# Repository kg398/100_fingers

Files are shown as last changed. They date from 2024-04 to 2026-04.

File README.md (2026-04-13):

# 100_fingers project: Parametric hand
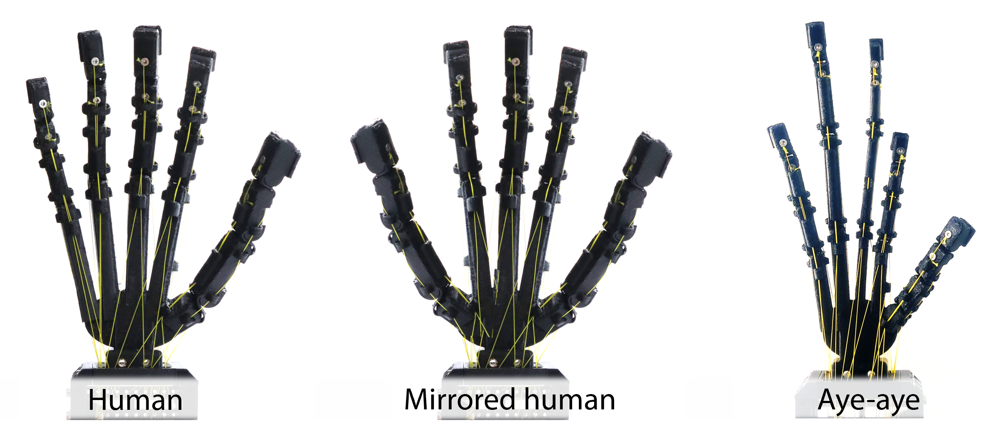
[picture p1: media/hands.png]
Human, mirrored human, and aye-aye hand designs and assemblies


Figure 1: Three example hands included in the initial release and presented in [(1)](#list-of-publications).

Generating large numbers of anatomical parameterised fingers and hands with OpenSCAD (https://openscad.org/).

## Changelog
- 10/12/2025: Overhaul of parameter definitions and modular bone generation, see section: Hand Customisation

## Intro
Code for generating the initial hand version and 3D files for reproduction and modular actuation.
The hand is designed for single-piece 3d printing with consumer-grade printers, enabling rapid customisation and large-scale real-world experimentation.
Additionally, the hand is designed to be uncomprimising with actuation. Five tendons per four degree of freedom finger allows full control. Though for simplicity, accessibility, and exploration of hand behaviours, the included actuation system examples rely heavily on underactuation by connecting the majority of tendons to passive springs.

### Summary of files
- /OpenSCAD: scripts for generating hands with OpenSCAD. parameters.scad for demo use and parameters for generating example hands
- /STLs: 3D files for 3D printable parts
  - /STLs/hands: three example hands generated from parameters.scad and example generated for visualisation (no_lig)
  - /STLs/actuation_box: 3D files for three examples of modular actuation (1 degree-of-freedom(dof)/synergy, 2 dof/synergy, 1 dof with switching modulation)
  - /STLs/manual_handles: 3D files for manual lever actuation and handles for 1 and 2 dof actuation boxes
- /build_guide: PDF, timelapse, and annotated video of build process for release v1.2
- /media: images from publication (in progress)

### Hand customisation
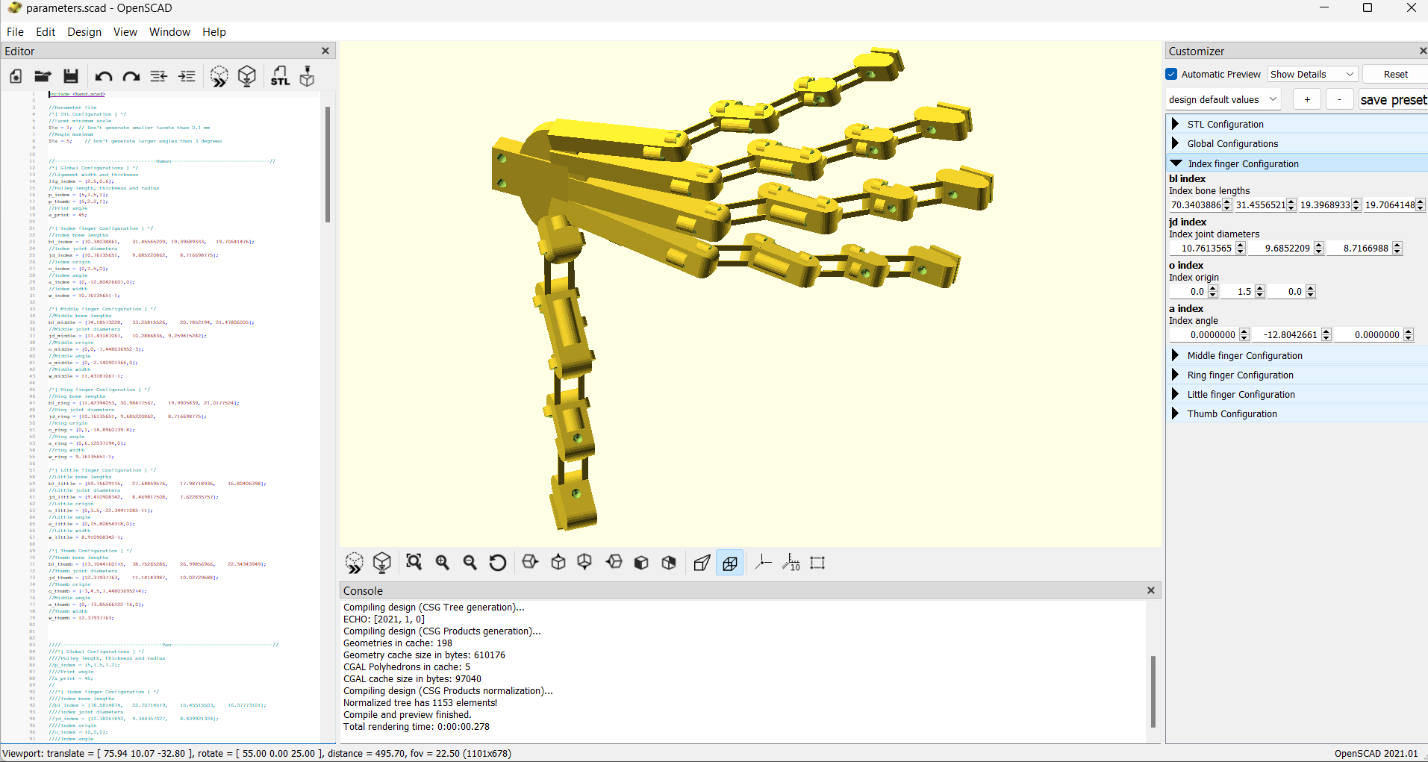
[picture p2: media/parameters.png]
Screenshot of parameters.scad in OpenSCAD


Figure 2: Hand parameters.

For basic customisation, parameters.scad can be modified to alter number of fingers/thumbs, predefined finger types (four_dof = anatomical, three_dof/two_dof = simplified examples), finger/thumb positions, orientations, curvature towards palm, all bone lengths/joint widths/diameters, pulley/ligament sizes.

For custom digits/bones built on existing primitives (e.g. for different tendon routings/degrees of freedom/no. bones), new configurations can be created (see digits.scad for configuration details). For new features, e.g. expanded types of joints/nails/etc., configurations must be extended and features manually defined in primitives.scad/modular_bone.

Parameters are separated into global and local. Three global params define number of fingers, number of thumbs and the overall hand curvature towards the palm (0 deg gives a flat hand all fingers in the same plane, 90 deg will keep fingers parallel as if wrapped around a cylinder).
Local parameters are organised into lists separated by digits (fingers vs. thumbs) and parameter types:
- finger_type: loads predefined finger configuration (four_dof = default anatomical finger). Must be at least 1 defined per n_fingers
- lig_[digit]: ligament width and thickness. If fewer pairs are defined than n_fingers, only the first pair will be used for all of that digit type
- p_[digit]: pulley length, internal radius, thickness. If fewer pairs are defined than n_fingers, only the first pair will be used for all of that digit type
- bl_[digit]: n bone lengths per digit where n is number of bones in digit type config. First element is closest to the palm 
- jd_[digit]: n+1 joint diameters per digit where n is number of bones in digit type config. First element is closest to the palm
- w_[digit]: n+1 joint widths per digit where n is number of bones in digit type config. First element is closest to the palm
- o_[digit]: 3 dof translation per digit. x = longitudinal (generally = 0), y = normal to palm, z = lateral to palm (main translation)
- a_[digit]: 3 dof rotation per digit, rx = unused, ry = digit rotation in a_print/hand curvature axis (normal to palm when a_print = 0, longitudinal axis when a_print = 90), rz = unused
  
## Fabrication instructions
### Hand assembly
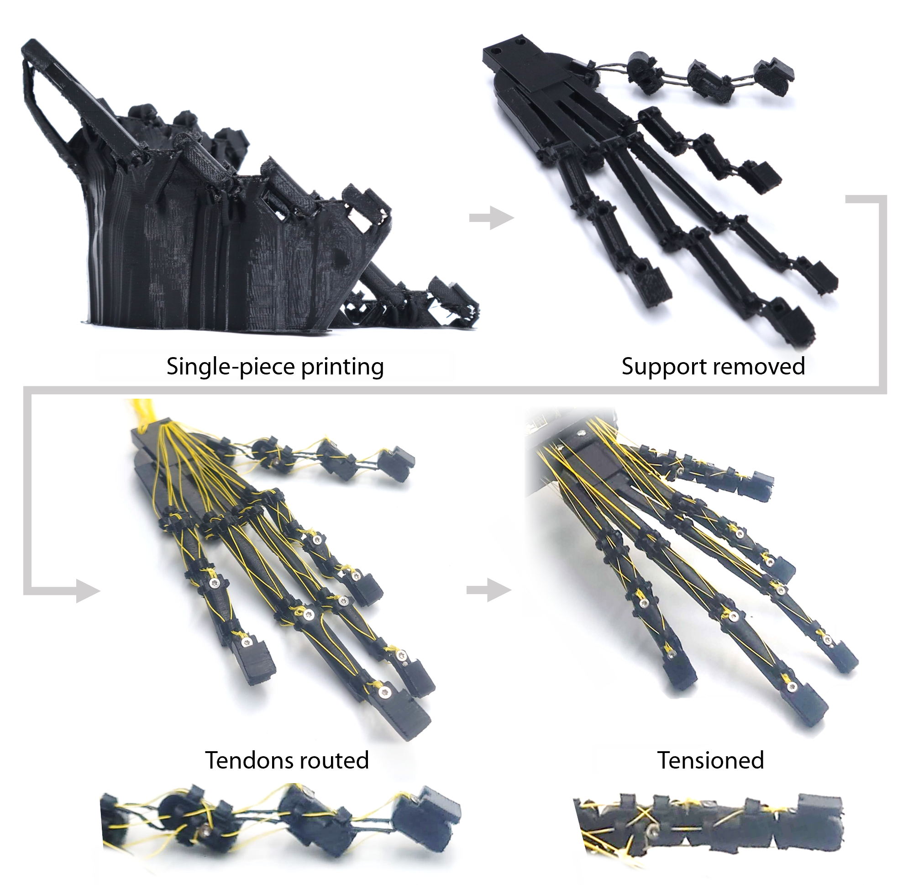
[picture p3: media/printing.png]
Steps for 3D printing and attaching tendons

Figure 3: Hand printing and assembly.

See /build_guide for more detailed fabrication tips and assembly information, and [bill of materials](#bill-of-materials) for basic acquisition requirements.

Hands can be printed via commercial FDM printers (Prusa/Creality/Craftbot/Raise3D tested). General printing requirements are: large build volume and semi-flexible materials. **Polypropylene** printing is recommended for good living hinge properties and relative ease of printing with a single extruder and standard temperatures. Print orientation is critical (palm should face down with fingertips closest to build plate and all ligament pairs flat relative to the build plate).

SLS printing is also suitable. Only polyamide (PA2200) has been tested, resulting in stiffer bones than polypropylene and a cleaner print. Orientation is less critical.

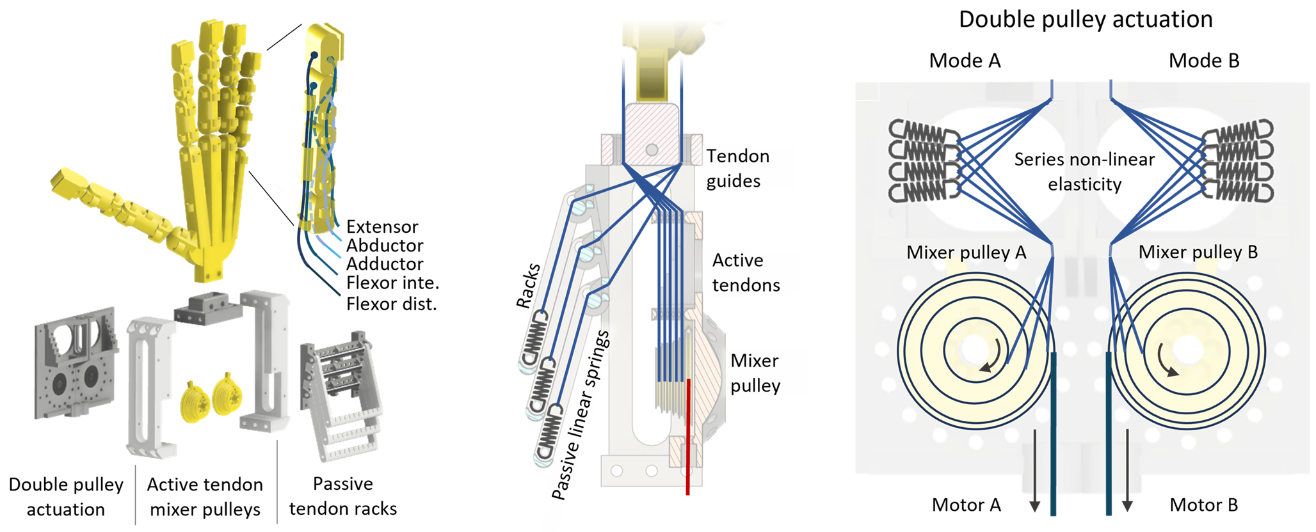
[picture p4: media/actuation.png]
Actuation box features and tendon routing paths


Figure 4: Tendon routing and actuation.

Once the hand is printed, tendons must be routed manually. Depending on application, braided nylon from 0.2--0.5mm diameter is suitable (0.2mm is easier to work with and results in less friction, though has lower load potential). Tie with self-tightening knots to countersunk M2 bolts following routing from Figure 4.

Actuation box is assembled as in Figure 4 with M2 and M3 bolts. All springs (passive tendon and active series elastic) should be approx 10--15mm free length and 0.06--1N/mm spring constant.

Human hand design with double pulley actuation gif

Figure 5: Whole assembly and manual actuation.

Manual handles allow testing of Bowden tube actuation and exploration of hand behaviours.

## In progress

Look out for future updates on:
- Hand design database and modelling/behaviour guide
- Parametric skin for printing/casting

## Licensing

- Code: General Public License v3.0 (GPLv3)
- 3D assets: Creative Commons Attribution (CC BY 4.0)

See /LICENSE for details.

## Appendix
### Demos
Resting state to ready joint state by tensioning all tendons gif

Figure 6: Joint organisation through tension.

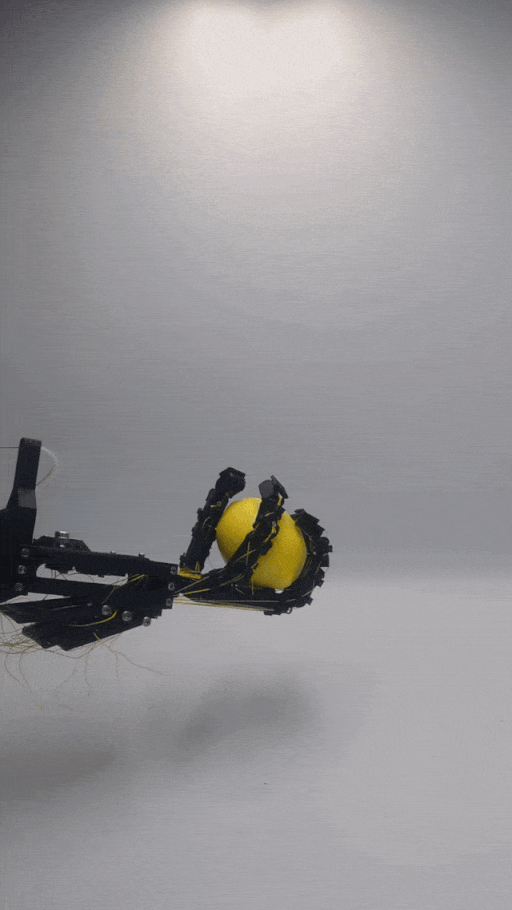
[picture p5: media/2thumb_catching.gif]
Throwing and catching a lemon with the mirrored hand design gif


Figure 7: Mirrored hand catching demo.

Manual picking up and using a computer mouse with the aye-aye hand design

Figure 8: Aye-aye hand demo.

### Bill of materials
Bill of materials for FDM printed human hand design with 1 dof actuation.

| Part  | Description | Quantity |
| --- | --- | ----: |
| Polypropylene filament  | Single-piece printed hand  | 80 (g) |
| M2x4 countersunk bolts | Tendon anchors | 21 |
| Braided fishing line, ~0.2 mm diameter, >20 kg load | Tendons | 10 (m) |
| ------------- | ------------- | ---- |
| PLA filament  | Actuation box printed parts  | 50 (g) |
| Extension springs (l: 10--15 mm; k: 0.1--1 N/mm) | Passive tendon mounting and SEA | 26 |
| 15x5x4 mm flanged bearing (flangeD/ID/W) | Actuation pulley mounting | 2 |
| 50x4mm smooth rod | Passive tendon bearing surface, e.g. aluminium | 3 |
| 60x1.5mm smooth rod | Passive tendon pins, e.g. fibreglass | 3 |
| Braided fishing line, ~1 mm diameter, >80 kg load | Actuation tendon |	0.3 (m) |
| M2x4 countersunk bolts |	SEA spring mount |	5 |
| M2x4 caphead |	Box assembly, passive tendon anchors, t-select |	3+21+1 |
| M2x8 caphead |	Box assembly and active tendon anchors |	6+6 |
| M2x10 caphead |	Box assembly and SEA pins |	2+2 |
| M2 nut |	Passive and active tendon anchors |	21+5 |
| M3x6 caphead |	Box assembly, wrist and handle mounting |	6+4+4 |
| M4x12 grub screw |	Hand mount |	2 |
| M5x16 caphead |	Pulley shaft |	1 |
| ------------- | ------------- | ---- |
| PLA filament  | Manual handle printed parts  | 100 (g) |
| 140x4 threaded rod, steel |	Tendon anchor and lever backbone |	1 |
| M4x25 caphead |	Anchor locking pin |	1 |
| M4 nut, square |	Tendon anchor |	4 |
| M5x25 caphead |	Lever shaft |	1 |

### List of publications
- (1) Gilday, K., Sirithunge, C., Iida, F., \& Hughes, J. (2025). Embodied manipulation with past and future morphologies through an open parametric hand design. Science Robotics, 10(102), eads6437. [/10.1126/scirobotics.ads6437](https://doi.org/10.1126/scirobotics.ads6437) (arxiv: [/10.48550/arXiv.2410.18633](https://doi.org/10.48550/arXiv.2410.18633))
- (2) Carlet, R., Gilday, K., & Hughes, J. (2025, April). Behaviour Range Optimization of the Dexterous Robotic Open Parametric Hand. In 2025 IEEE 8th International Conference on Soft Robotics (RoboSoft) (pp. 1-7). IEEE. [/10.1109/RoboSoft63089.2025.11020976](https://doi.org/10.1109/RoboSoft63089.2025.11020976)
- (3) Gilday, K., Pyeon, D., Dhanush, S., Cho, K. J., & Hughes, J. (2024). Exploiting passive behaviours for diverse musical playing using the parametric hand. Frontiers in Robotics and AI, 11, 1463744. [/10.3389/frobt.2024.1463744](https://doi.org/10.3389/frobt.2024.1463744)

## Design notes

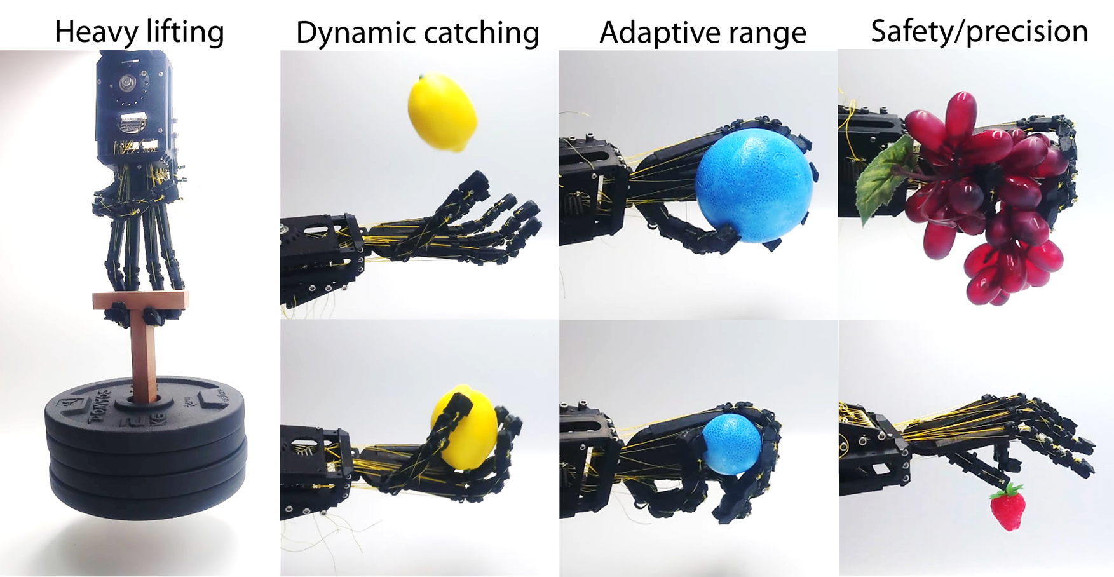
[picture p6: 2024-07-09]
media/functions.png

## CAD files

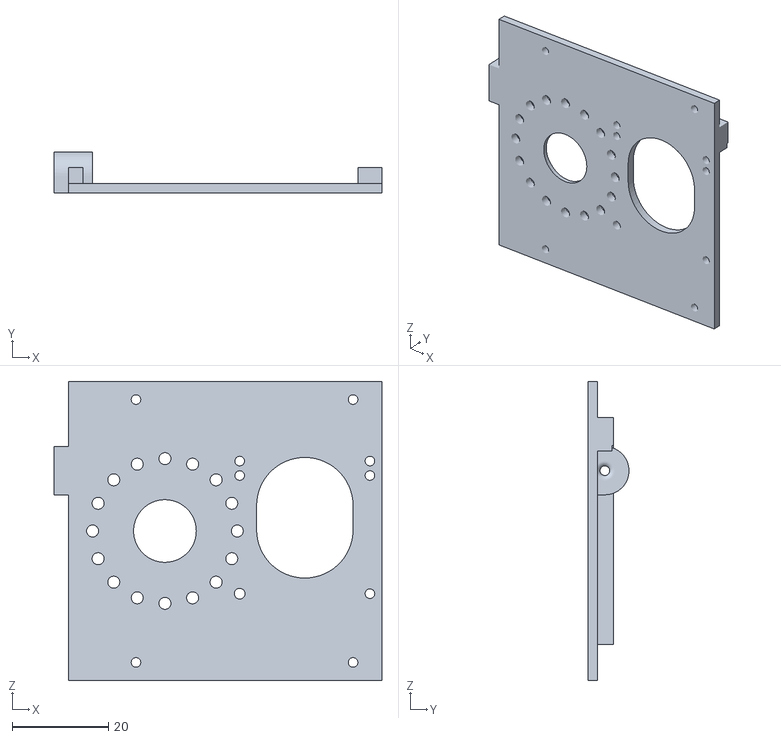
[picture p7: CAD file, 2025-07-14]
STLs/actuation_box/1dof/pulley_base.stl
68.0 x 8.49 x 62.0

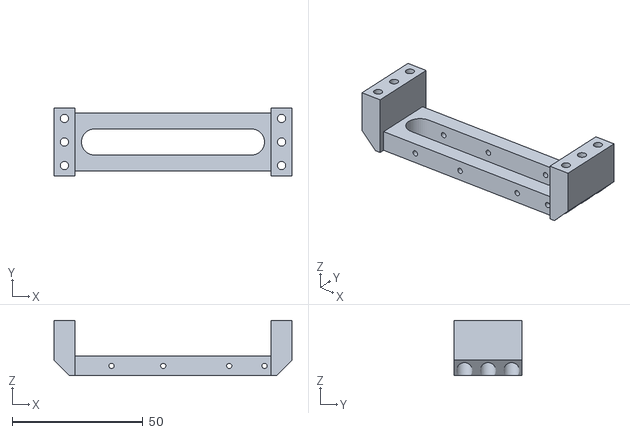
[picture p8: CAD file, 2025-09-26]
STLs/actuation_box/2dof/side_panel_left.stl
91.0 x 26.0 x 21.2

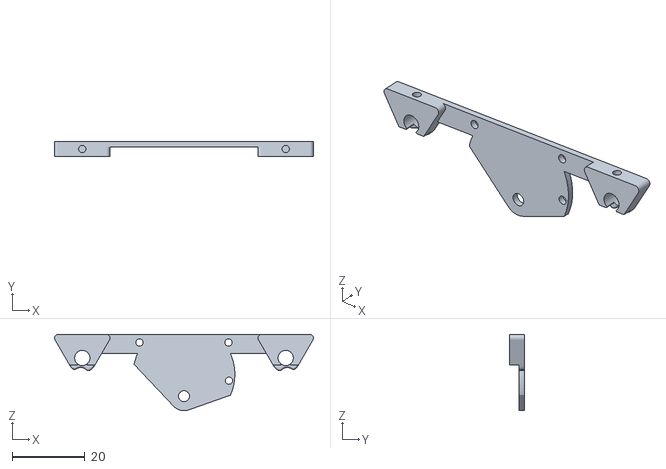
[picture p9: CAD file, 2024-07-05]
STLs/actuation_box/switching/switching_support_v2.stl
71.3 x 4.00 x 21.0

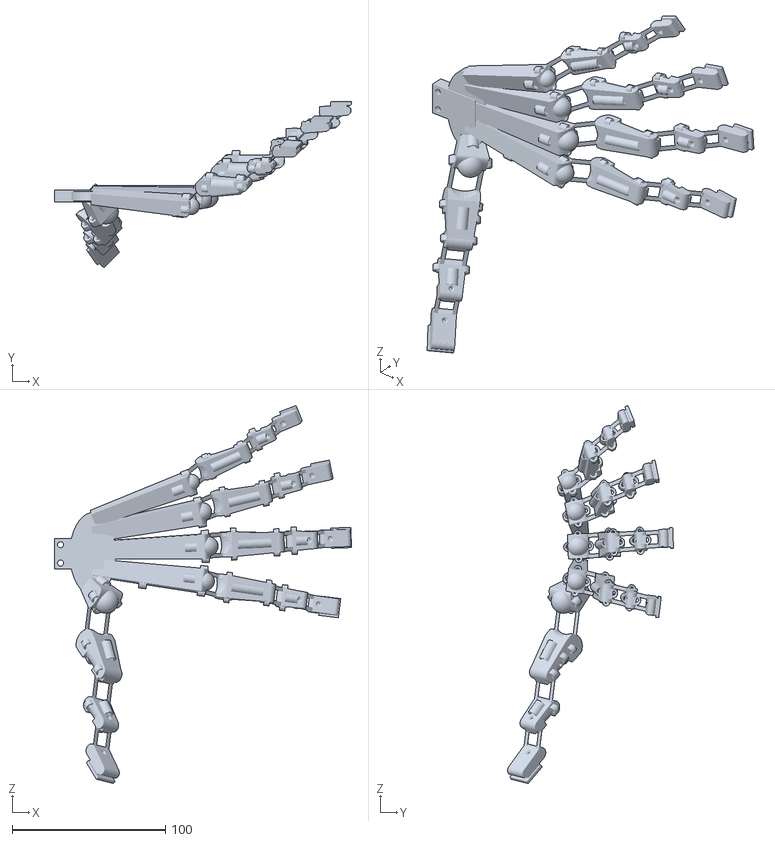
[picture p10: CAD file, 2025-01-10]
STLs/hands/human_hand_v4.stl
194.0 x 108.4 x 246.8

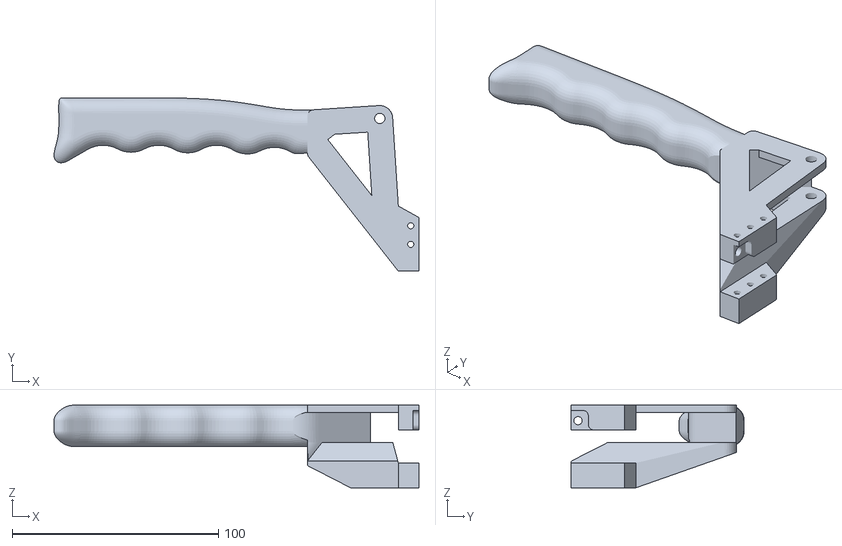
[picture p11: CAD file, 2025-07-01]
STLs/manual_handles/1dof/handle.stl
176.8 x 84.0 x 40.0

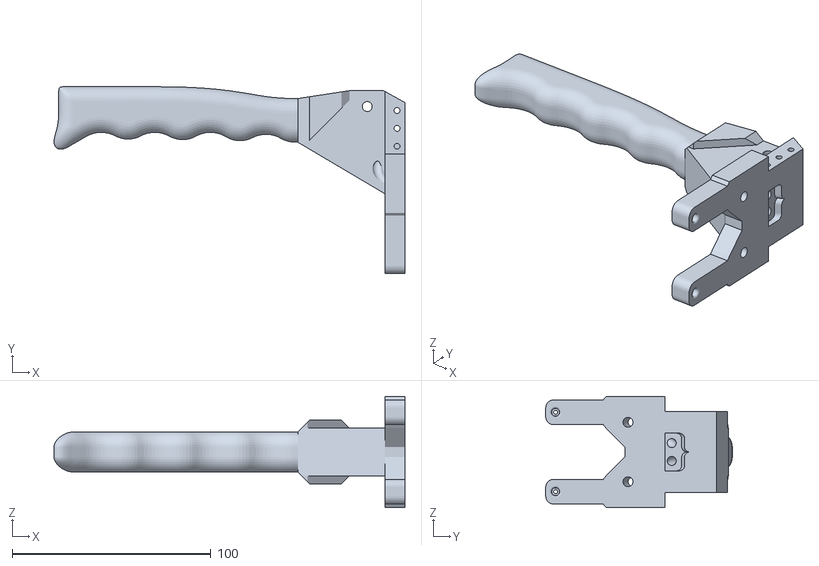
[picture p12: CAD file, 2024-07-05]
STLs/manual_handles/2dof/handle_double.stl
176.8 x 94.0 x 56.0

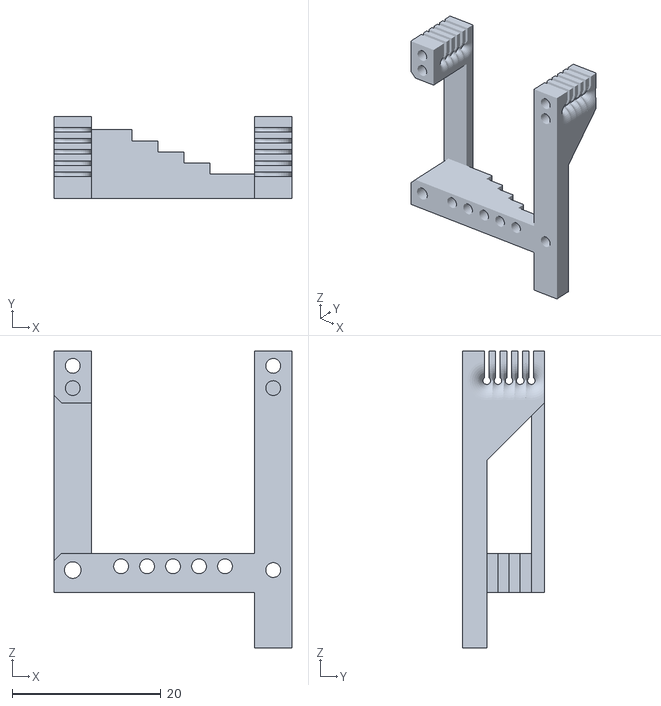
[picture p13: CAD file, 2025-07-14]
STLs/actuation_box/1dof/sea.stl
32.0 x 11.0 x 40.0

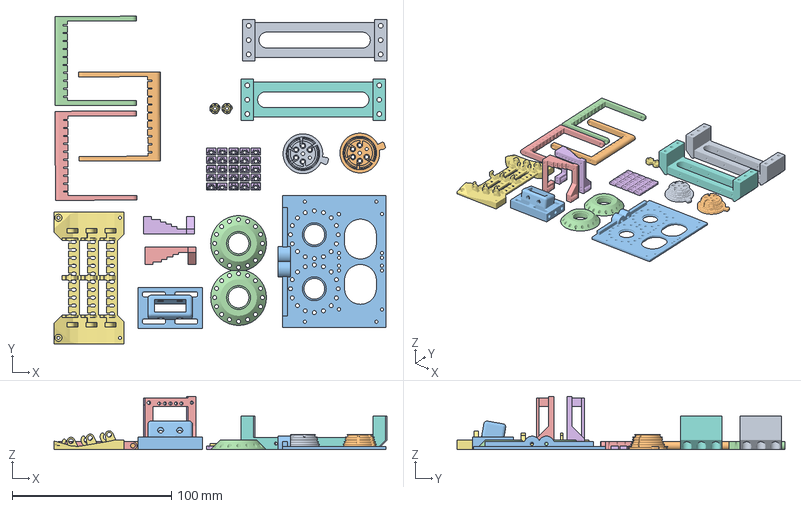
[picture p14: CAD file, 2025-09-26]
STLs/actuation_box/2dof/bambu_plate.3mf
209.4 x 206.0 x 33.5 mm
pulley_default.stl
pulley_default_mirror.stl
pulley_plate.stl
pulley_plate_bearing.stl
pulley_plate_sea.stl
pulley_plate_sea_mirror.stl
rack_mount.stl
side_panel_left.stl
side_panel_right.stl
spring_rack.stl x 3
wrist_mount_10deg.stl
Assembly x 2

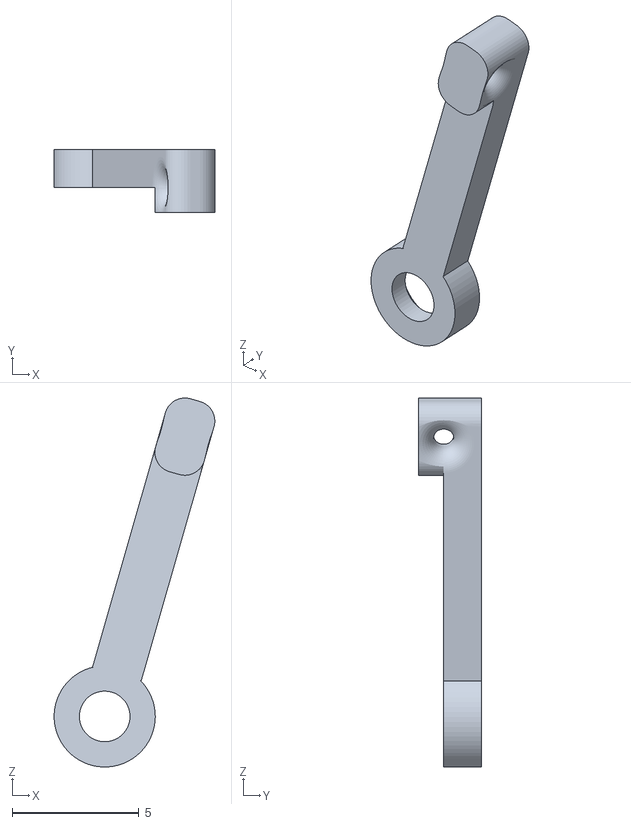
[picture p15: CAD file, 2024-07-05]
STLs/actuation_box/switching/rigid_spring.stl
6.35 x 2.50 x 14.6

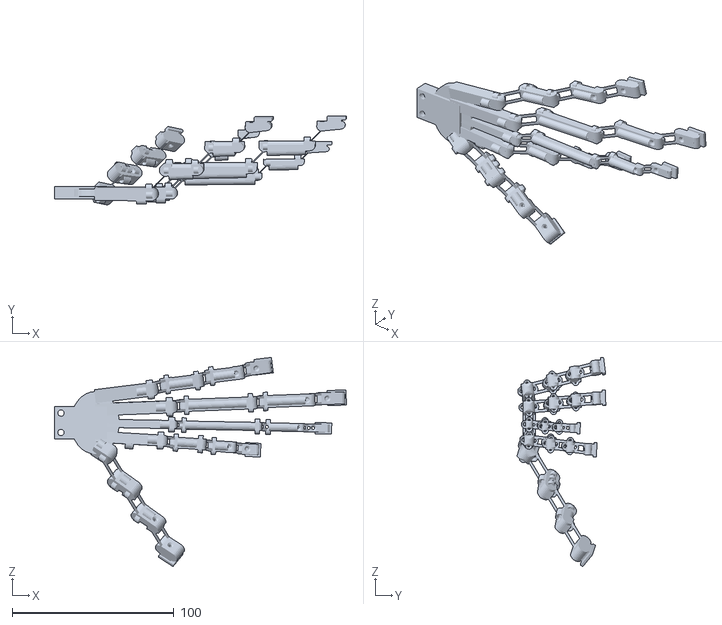
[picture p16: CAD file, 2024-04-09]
STLs/hands/daubentonia_v3.stl
180.3 x 54.8 x 129.2

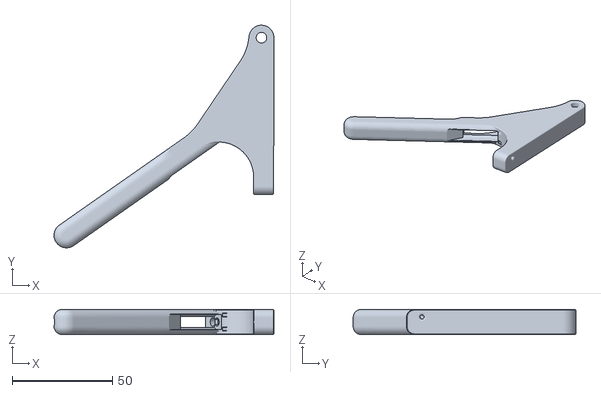
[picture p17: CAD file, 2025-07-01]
STLs/manual_handles/1dof/lever.stl
109.8 x 111.1 x 12.5

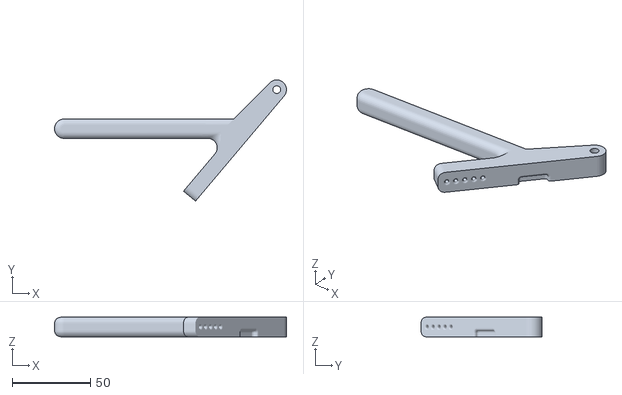
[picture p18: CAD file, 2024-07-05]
STLs/manual_handles/2dof/lever_double.stl
148.7 x 77.7 x 12.5

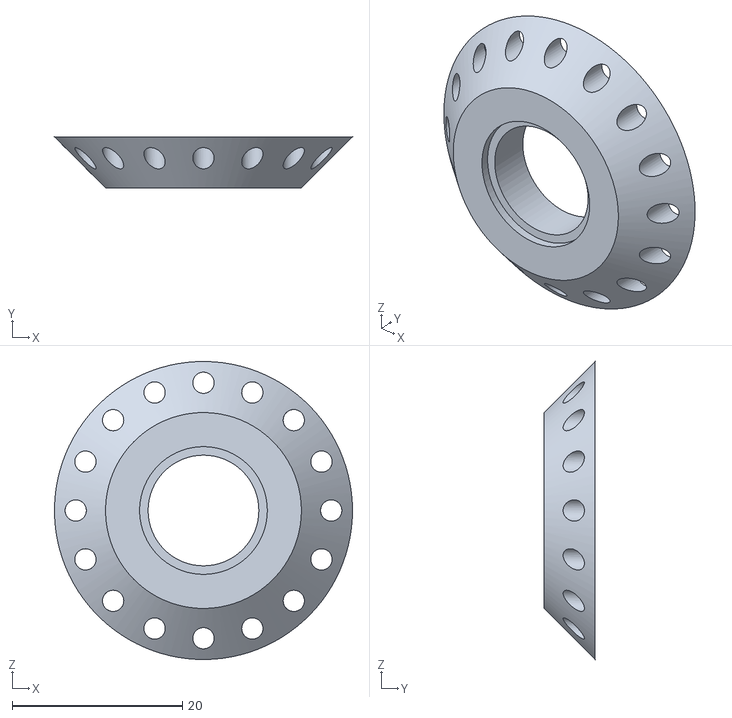
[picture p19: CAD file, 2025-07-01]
STLs/actuation_box/1dof/bearing_block.stl
35.0 x 6.00 x 35.0

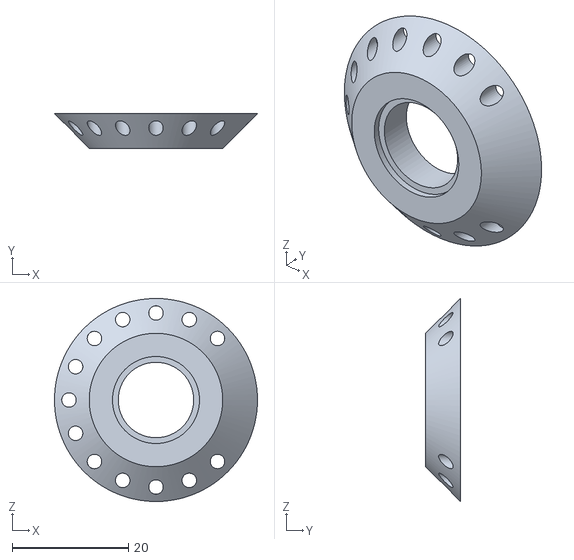
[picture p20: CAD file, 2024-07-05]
STLs/actuation_box/switching/pulley_spacer_v2.stl
35.0 x 6.00 x 35.0

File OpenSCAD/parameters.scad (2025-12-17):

include <hand.scad>

//Parameter file
//Uncomment block to use various predefined examples
//Hands generated with call functions at the end of this file

//Digit type names
four_dof = 0;
four_dof_thumb = 1;
three_dof = 2;
three_dof_thumb = 3;
two_dof = 4;
two_dof_thumb = 5;

/*[ STL Configuration ] */
//Facet minimum scale
$fs = 1;  // Don't generate smaller facets than 0.1 mm
//Angle maximum
$fa = 10;    // Don't generate larger angles than 3 degrees


//////--------------------------------Human_v2---------------------------------//
/*[ Global Configurations ] */
//Number of fingers (0--?)
n_fingers = 4;
// Number of thumbs (0--2)
n_thumbs = 1;
//Print angle/hand inward curvature
a_print = 45;

/*[ Finger Configuration ] */
//Finger types
type_finger = [four_dof,
               four_dof,
               four_dof,
               four_dof];
//Finger ligament width and thickness
lig_finger = [[2.5,0.6]];
//Finger pulley length, thickness and radius
p_finger = [[5,1.5,1]];
//Finger bone lengths
bl_finger = [[80,	38, 20,	20],
             [82,	41,	20.5,	20.5],
             [79,	38,	19,	19],
             [74,	35,	17,	17]];
//Finger joint diameters
base_jd_finger = [[12.5],
                  [14],
                  [12.5],
                  [11]];
jd_finger = base_jd_finger*[[0.7, 1, 0.6, 0.5, 0.4]];
//Finger origins
o_finger = [[0,1.5,0],
            [0,0,-12],
            [0,1,-24],
            [0,3.5,-34]];
//Finger angles
a_finger = [[0,-10,0],
            [0,3,0],
            [0,16,0],
            [0,30,0]];
//Finger widths
base_w_finger = [[15],
                 [16],
                 [15],
                 [13]];
w_finger = base_w_finger*[[0.7, 1, 0.8, 0.7, 0.7]];

/*[ Thumb Configuration ] */
//Thumb types
type_thumb = [four_dof_thumb,
              four_dof_thumb];
//Thumb ligament width and thickness
lig_thumb = [[2.5,0.6]];
//Thumb pulley length, thickness and radius
p_thumb = [[5,2.2,1]];
//Thumb bone lengths
bl_thumb = [[25,	35,	25,	25],
            [25,	35,	25,	25]];
//Thumb joint diameters
base_jd_thumb = [[16],
                 [16]];
jd_thumb = base_jd_thumb*[[0.7, 1, 0.6, 0.5, 0.4]];
//Thumb origins
o_thumb = [[-3,5.5,15],
           [-3,5.5,-45]];
//Thumb angles
a_thumb = [[0,-100,0],
           [0,100,0]];
//Thumb widths
base_w_thumb = [[20],
                [20]];
w_thumb = base_w_thumb*[[0.7, 1, 0.8, 0.7, 0.7]];





//-----------------------------modular hand export------------------------//
//param1=3; //palm/digit type
//param2=0; //digit id
////palm = 0;
////finger = 1;
////thumb = 2;
////all = 3;
////openscad.com -o "palm_test.stl" -D "param1=0" -D "param2=0" parameters.scad && 
////openscad.com -o "finger0_test.stl" -D "param1=1" -D "param2=0" parameters.scad &&
////openscad.com -o "thumb0_test.stl" -D "param1=2" -D "param2=0" parameters.scad &&
//
//echo(param1);
//echo(param2);

//-----------basic verification that finger/thumb definitions exist-------//
assert(len(type_finger)>=n_fingers && len(bl_finger)>=n_fingers && len(jd_finger)>=n_fingers && len(o_finger)>=n_fingers && len(a_finger)>=n_fingers && len(w_finger)>=n_fingers, "Must be parameters defined for each of n_fingers");
assert(len(type_thumb)>=n_thumbs && len(bl_thumb)>=n_thumbs && len(jd_thumb)>=n_thumbs && len(o_thumb)>=n_thumbs && len(a_thumb)>=n_thumbs && len(w_thumb)>=n_thumbs, "Must be parameters defined for each of n_thumbs");
//-----------------------------generate from params-----------------------//
rotate([180,0,0]){
    hand();             // standard version for printing
//    hand_nolig();       // non-print version only for visualisation
//    single_finger();    // just generate index finger
//    hand_modular(model=param1,digit_id=param2);  // version where palm and fingers can be printed separately (model=all/palm/finger/thumb, digit_id=finger/thumb list index)
}
    
//---------------------------------camera setup---------------------------//
//$vpr = [ 85.10, 0.00, 8.90 ];
//$vpt = [ 2.93, -42.38, 87.58 ];
//$vpd = 623.64;
//$vpf = 22.50;

////for animation: fps 30, steps 360
//$vpr = [ 71.10, 0.00, 360*$t ];
//$vpt = [ 0, 0, 50 ];
//$vpd = 561.28;
//$vpf = 22.50;


echo(version());

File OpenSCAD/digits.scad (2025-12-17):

include <primitives.scad>

////Facet minimum scale
//$fs = 0.2;  // Don't generate smaller facets than 0.1 mm
////Angle maximum
//$fa = 5;    // Don't generate larger angles than 3 degrees

////Bone configurations
//[joint1 type, joint2 type, flexor pulley type, extensor pulley type, abd pulley type, fillet type, flexor anchor type, extensor anchor type, opposition anchor, opposition pulley]
//0
//joint 1 type:
//          0   -   base (flat)
//          1   -   1dof (hyp constrained)
//          2   -   2dof
//
//          4   -   base (modular)
//          5   -   base (modular negative)
//1
//joint 2 type:
//          0   -   none
//          1   -   1dof (hyp constrained)
//          2   -   2dof
//          3   -   tip (with nail) (joint 2 only)
//
//
//2
//flex pulley type
//          0   -   none
//          1   -   joint 1 only (not implemented)
//          2   -   joint 2 only
//          3   -   both joints
//3
//ext pulley type
//          0   -   none
//          1   -   joint 1 only
//          2   -   joint 2 only
//          3   -   both joints
//4
//abd pulley type
//          0   -   none
//          1   -   joint 1 only
//          2   -   joint 2 only
//          3   -   both joints
//5
//fillet type
//          0   -   none
//          1   -   extensor side fillet
//6
//flexor anchor type
//          0   -   none
//          1   -   joint 1 anchor
//          2   -   joint 2 anchor
//7
//extensor anchor type
//          0   -   none
//          1   -   joint 1 anchor
//          2   -   central anchor
//8
//ligament type
//          0   -   none
//          1   -   default
//9
//thumb opposition flag
//          0   -   false
//          1   -   true
//10
//opposition pulley
//          0   -   false
//          1   -   true
//assembly jig holes
//          0   -   false
//          1   -   meta-type (hole 15mm from tip)
//          2   -   prox-type (central hole)
//          3   -   inte-type (central hole offset)
//          4   -   dist-type (nail hole)



////Finger type configurations
//dof4:
dof4_config =              [[0,2,2,2,2,0,0,0,0,0,1,1],//metacarpal
                            [2,1,3,3,3,1,0,0,1,0,0,2],//proximal
                            [1,1,3,2,1,1,2,1,1,0,0,3],//intermediate
                            [1,3,0,0,0,0,1,1,1,0,0,4]];//distal
dof4_thumb_config =        [[0,2,2,2,2,0,0,0,0,0,0,1],//metacarpal
                            [2,1,3,3,3,1,0,0,1,1,0,2],//proximal
                            [1,1,3,2,1,1,2,1,1,0,0,3],//intermediate
                            [1,3,0,0,0,0,1,1,1,0,0,4]];//distal
dof3_config =              [[0,2,2,2,2,0,0,0,0,0,1,0],                
                            [2,1,3,2,1,1,0,1,1,0,0,0],
                            [1,3,0,0,0,0,1,1,1,0,0,0]];
dof3_thumb_config =        [[0,2,2,2,2,0,0,0,0,0,0,0],                
                            [2,1,3,2,1,1,0,1,1,1,0,0],
                            [1,3,0,0,0,0,1,1,1,0,0,0]];
dof2_config =              [[0,1,2,2,0,0,0,0,0,0,1,0],                
                            [1,1,3,2,0,0,0,1,1,0,0,0],
                            [1,3,0,0,0,0,1,1,1,0,0,0]];
dof2_thumb_config =        [[0,1,2,2,0,0,0,0,0,0,0,0],                
                            [1,1,3,2,0,0,0,1,1,1,0,0],
                            [1,3,0,0,0,0,1,1,1,0,0,0]];


//finger(type = 0,bl_list=[50,20,20,20],jd_list=[8,10,8,7,6],w_list=[10,12,10,9,8],lig=[2.5,0.6],p=[5,1,1.5],ang=45,thumb_adj1=0,thumb_adj2=0,thumb_side = 0);
//finger module
//type -> predefined finger type configuration id, see function bone_configs(type)
//bl_list -> list of bone lengths, size should match config
//jd_list -> diameter of each joint, size should match config+1
//w_list -> width of each joint, size should match config+1
//lig -> ligament params [width, thickness]
//p -> pulley params [length, radius, thickness]
//ang -> ligament angle, use for printing bones in different orientations
//thumb_adj -> dz for adjacent thumb opposition pulley
//thumb side -> thumb adjacent on left/right/both (0/1/2)
module finger(type,bl_list,jd_list,w_list,lig,p,ang,thumb_adj1=0,thumb_adj2=0,thumb_side=0){
    config_list = bone_configs(type);
    rotate([0,0,ang]){
        union()
            nested_bone(0,config_list,bl_list,jd_list,w_list,lig,p,ang,thumb_adj1,thumb_adj2,thumb_side);
    }
}
// (private) recursive function for staggered bone offsets
module nested_bone(level,config_list,bl_list,jd_list,w_list,lig=[2.5,0.6],p=[5,1,1.5],ang=45,thumb_adj1=0,thumb_adj2=0,thumb_side=0){
    mcp_ang=30;
    dr=(w_list[level]-w_list[level]*sin(acos((w_list[level]/2-lig[0])/w_list[level])))/jd_list[level];
    trans = level == 0 ? [0,0,0]:
                        config_list[level][0]==2 ? [bl_list[level-1]+(-1+(0.5+dr)*cos(mcp_ang))*jd_list[level]+sqrt((0.5*jd_list[level]*(1+(1+dr)*sin(mcp_ang)))^2+(jd_list[level]*(1-(0.5+dr/2)*cos(mcp_ang)))^2)*cos(ang),lig[1]+(-0.5-(0.5+dr)*sin(mcp_ang))*jd_list[level]-sqrt((0.5*jd_list[level]*(1+(1+dr)*sin(mcp_ang)))^2+(jd_list[level]*(1-(0.5+dr/2)*cos(mcp_ang)))^2)*sin(ang)-2*lig[1]*sin(ang)*sin(ang),0]:
                                            [bl_list[level-1]-jd_list[level]+(0.5*PI*jd_list[level]+lig[1])*cos(ang),-jd_list[level]+lig[1]+0.2-(0.5*PI*jd_list[level]+lig[1])*sin(ang),0];
    translate(trans){
        modular_bone(config_list[level],bl_list[level],[jd_list[level],jd_list[level+1]],[w_list[level],w_list[level+1]],lig,p,ang,thumb_adj1,thumb_adj2,thumb_side);
        if(level<len(config_list)-1){
            nested_bone(level+1,config_list,bl_list,jd_list,w_list,lig,p,ang,thumb_adj1,thumb_adj2,thumb_side);
        }
    }
}
//load predefined bone configuration lists
function bone_configs(type) =
    type == 0 ? dof4_config:
    type == 1 ? dof4_thumb_config:
    type == 2 ? dof3_config:
    type == 3 ? dof3_thumb_config:
    type == 4 ? dof2_config:
    type == 5 ? dof2_thumb_config:0;

//palm(-36.5,17.5,2.5,10);
//palm module
//min_x -> furthest right finger/thumb coord 
//max_x -> furthest left finger/thumb coord 
//min_y -> closest on dorsal side coord
//max_y -> closest on palmar side coord
module palm(min_x,max_x,min_y,max_y){
    translate([0,min_y,(max_x+min_x)/2]) rotate([-90,0,0])
        union(){
            // palm-finger connection
            dz = 30;
            resize(newsize=[dz,max_x-min_x,max_y-min_y]) cylinder(10,5,5);
            // wrist interface
            translate([-dz/2-10,-10,(max_y-min_y)/2-4]){
                difference(){
                    cube([10+0.75*dz,20,8]);
                    translate([4,4,-0.1])
                        cylinder(8.2,2,2);
                    translate([4,16,-0.1])
                        cylinder(8.2,2,2);
                }
            }
        }
}

//finger module with no ligaments (only for visulaisation)
module finger_nolig(type,bl_list,jd_list,w_list,lig,p,ang,thumb_adj1=0,thumb_adj2=0,thumb_side=0){
    config_list = bone_configs(type);
    //turn off ligaments
    lig_filter_matrix = [for(i=[0:1:len(config_list[0])-1]) [for(j=[0:1:len(config_list[0])-1]) i==j && i!=8 ? 1:0]];
    config_list_nolig = config_list*lig_filter_matrix;
    rotate([0,0,ang]){
        union()
            nested_bone_nolig(0,config_list_nolig,bl_list,jd_list,w_list,lig,p,ang,thumb_adj1,thumb_adj2,thumb_side);
    }
}
// (private) recursive function for staggered bone offsets with no ligaments
module nested_bone_nolig(level,config_list,bl_list,jd_list,w_list,lig=[2.5,0.6],p=[5,1,1.5],ang=45,thumb_adj1=0,thumb_adj2=0,thumb_side=0){
    trans = level == 0 ? [0,0,0]:[bl_list[level-1]+lig[1],0,0];
    translate(trans){
        modular_bone(config_list[level],bl_list[level],[jd_list[level],jd_list[level+1]],[w_list[level],w_list[level+1]],lig,p,ang,thumb_adj1,thumb_adj2,thumb_side);
        if(level<len(config_list)-1){
            nested_bone_nolig(level+1,config_list,bl_list,jd_list,w_list,lig,p,ang,thumb_adj1,thumb_adj2,thumb_side);
        }
    }
}
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

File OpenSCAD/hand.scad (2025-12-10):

include <digits.scad>
//takes variables defined in parameters.scad and generates hand assemblies

//----------------------Finger----------------------//
module single_finger(){
    union(){
        // finger defined by first in finger list (e.g. index finger)
        rotate([0,0,-a_print])
            finger(type_finger[0],
                       bl_finger[0],
                       jd_finger[0],
                       w_finger[0],
                       lig_finger[0],
                       p_finger[0],
                       a_print);
        // wrist interface
        translate([-10,jd_finger[0][0]-8,10]) rotate([-90,0,0])
            difference(){
                cube([10.1,20,8]);
                translate([4,4,-0.1])
                    cylinder(8.2,2,2);
                translate([4,16,-0.1])
                    cylinder(8.2,2,2);
            }
    }
}

//-----------------------Hand-----------------------//
module hand(){
    union(){
        // Fingers
        for(i=[0:1:n_fingers-1]){
            //if setting gloabl finger/thumb ligament/pulley params
            lig = i<len(lig_finger)?lig_finger[i]:lig_finger[0];
            p = i<len(p_finger)?p_finger[i]:p_finger[0];
            //if adjacent to a thumb, include opposition pulley location info
            dz1 = i==0 && n_thumbs>0 ? 
                        (bl_thumb[0][0]+jd_thumb[0][0]-p[0]>bl_finger[i][0]-jd_finger[i][1]/2-p[0]*2 ? bl_finger[i][0]-jd_finger[i][1]/2-p[0]*2.5 : bl_thumb[0][0]+jd_thumb[0][0]-p[0]):
                        0;
            dz2 = i==n_fingers-1 && n_thumbs>1 ? 
                        (bl_thumb[1][0]+jd_thumb[1][0]-p[0]>bl_finger[i][0]-jd_finger[i][1]/2-p[0]*2 ? bl_finger[i][0]-jd_finger[i][1]/2-p[0]*2.5 : bl_thumb[1][0]+jd_thumb[1][0]-p[0]):
                        0;
            //generate finger from parameters and configuration given by type (see digits.scad/bone_config(type))
            translate(o_finger[i]) rotate([0,0,-a_print]) rotate(a_finger[i])
                finger(type_finger[i],
                       bl_finger[i],
                       jd_finger[i],
                       w_finger[i],
                       lig,
                       p,
                       a_print,
                       thumb_adj1=dz1,
                       thumb_adj2=dz2,
                       thumb_side = n_fingers==1? 2:i==0?0:1);
        }
        // Thumbs
        for(i=[0:1:n_thumbs-1]){
            //if setting gloabl finger/thumb ligament/pulley params
            lig = i<len(lig_thumb)?lig_thumb[i]:lig_thumb[0];
            p = i<len(p_thumb)?p_thumb[i]:p_thumb[0];
            //thumb reuses finger module with its own configuration defined by type
            translate(o_thumb[i]) rotate([0,0,-a_print]) rotate(a_thumb[i])
                finger(type_thumb[i],
                       bl_thumb[i],
                       jd_thumb[i],
                       w_thumb[i],
                       lig,
                       p,
                       a_print,
                       thumb_side=i);
        }
        // Palm
        {
        //scale to max width (both thumbs if they exist, or first/last finger)
        y_mask = [[0],
                  [1],
                  [0]];
        base_mask = [[1],
                  [0],
                  [0],
                  [0],
                  [0]];
        min_x = n_thumbs>1 ? o_thumb[1][2]:o_finger[n_fingers-1][2];
        max_x = n_thumbs>0 ? o_thumb[0][2]:o_finger[0][2];
        min_y = n_thumbs>0 && n_fingers>0 ? max(max(o_finger*y_mask)[0],max(o_thumb*y_mask)[0]-5):
                                   (n_thumbs>0 ? max(o_thumb*y_mask)[0]-5:max(o_finger*y_mask)[0]);
        max_y = n_thumbs>0 && n_fingers>0 ? 1+min(min(jd_finger*base_mask+o_finger*y_mask)[0],min(jd_thumb*base_mask+o_thumb*y_mask)[0]):
                                    (n_thumbs>0 ? 1+min(jd_thumb*base_mask+o_thumb*y_mask)[0]:1+min(jd_finger*base_mask+o_finger*y_mask)[0]);
        palm(min_x-2.5,max_x+2.5,min_y,max_y);                
        }
    }
}

//------------------Hand --- no lig------------------//
module hand_nolig(){
    union(){
        // Fingers
        for(i=[0:1:n_fingers-1]){
            //if setting gloabl finger/thumb ligament/pulley params
            lig = i<len(lig_finger)?lig_finger[i]:lig_finger[0];
            p = i<len(p_finger)?p_finger[i]:p_finger[0];
            //if adjacent to a thumb, include opposition pulley location info
            dz1 = i==0 && n_thumbs>0 ? 
                        (bl_thumb[0][0]+jd_thumb[0][0]-p[0]>bl_finger[i][0]-jd_finger[i][1]/2-p[0]*2 ? bl_finger[i][0]-jd_finger[i][1]/2-p[0]*2.5 : bl_thumb[0][0]+jd_thumb[0][0]-p[0]):
                        0;
            dz2 = i==n_fingers-1 && n_thumbs>1 ? 
                        (bl_thumb[1][0]+jd_thumb[1][0]-p[0]>bl_finger[i][0]-jd_finger[i][1]/2-p[0]*2 ? bl_finger[i][0]-jd_finger[i][1]/2-p[0]*2.5 : bl_thumb[1][0]+jd_thumb[1][0]-p[0]):
                        0;
            //generate finger from parameters and configuration given by type (see digits.scad/bone_config(type))
            translate(o_finger[i]) rotate([0,0,-a_print]) rotate(a_finger[i])
                finger_nolig(type_finger[i],
                       bl_finger[i],
                       jd_finger[i],
                       w_finger[i],
                       lig,
                       p,
                       a_print,
                       thumb_adj1=dz1,
                       thumb_adj2=dz2,
                       thumb_side = n_fingers==1? 2:i==0?0:1);
        }
        // Thumbs
        for(i=[0:1:n_thumbs-1]){
            //if setting gloabl finger/thumb ligament/pulley params
            lig = i<len(lig_thumb)?lig_thumb[i]:lig_thumb[0];
            p = i<len(p_thumb)?p_thumb[i]:p_thumb[0];
            //thumb reuses finger module with its own configuration defined by type
            translate(o_thumb[i]) rotate([0,0,-a_print]) rotate(a_thumb[i])
                finger_nolig(type_thumb[i],
                       bl_thumb[i],
                       jd_thumb[i],
                       w_thumb[i],
                       lig,
                       p,
                       a_print,
                       thumb_side=i);
        }
        // Palm
        {
        //scale to max width (both thumbs if they exist, or first/last finger)
        y_mask = [[0],
                  [1],
                  [0]];
        base_mask = [[1],
                  [0],
                  [0],
                  [0],
                  [0]];
        min_x = n_thumbs>1 ? o_thumb[1][2]:o_finger[n_fingers-1][2];
        max_x = n_thumbs>0 ? o_thumb[0][2]:o_finger[0][2];
        min_y = n_thumbs>0 && n_fingers>0 ? max(max(o_finger*y_mask)[0],max(o_thumb*y_mask)[0]-5):
                                   (n_thumbs>0 ? max(o_thumb*y_mask)[0]-5:max(o_finger*y_mask)[0]);
        max_y = n_thumbs>0 && n_fingers>0 ? 1+min(min(jd_finger*base_mask+o_finger*y_mask)[0],min(jd_thumb*base_mask+o_thumb*y_mask)[0]):
                                    (n_thumbs>0 ? 1+min(jd_thumb*base_mask+o_thumb*y_mask)[0]:1+min(jd_finger*base_mask+o_finger*y_mask)[0]);
        palm(min_x-2.5,max_x+2.5,min_y,max_y);                
        }
    }
}
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

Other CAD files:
STLs/actuation_box/2dof/side_panel_right.stl
STLs/hands/double_thumb_v3.stl
STLs/actuation_box/1dof/panel_left.stl
STLs/actuation_box/2dof/pulley_plate_bearing.stl
OpenSCAD/primitives.scad
OpenSCAD/pulley.scad
OpenSCAD/skin.scad
STLs/actuation_box/1dof/panel_right.stl
STLs/actuation_box/1dof/pulley_parametric.stl
STLs/actuation_box/2dof/pulley_default.stl
STLs/actuation_box/2dof/pulley_default_mirror.stl
STLs/actuation_box/2dof/pulley_plate.stl
STLs/actuation_box/2dof/pulley_tselect.stl
STLs/actuation_box/2dof/spring_rack.stl
STLs/actuation_box/2dof/tendon_hook_v4.stl
STLs/actuation_box/2dof/wrist_mount_10deg.stl
STLs/actuation_box/switching/hand_couple.stl
STLs/actuation_box/switching/pin_holder.stl
STLs/actuation_box/switching/pulley_plate_v2.stl
STLs/actuation_box/switching/pulley_stretched.stl
STLs/actuation_box/switching/rack.stl
STLs/actuation_box/switching/rack_lever.stl
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

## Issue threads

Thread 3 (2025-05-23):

request update of the step-by-step instructions

minnyqiu, 2025-05-23:
Hi, I am trying to use the 'parameters.scad' file to export the STL file and print the hand, and after rendering, there is a warning: 'Object may not be a valid 2-manifold and may need repair!' Please advise if it will affect the printing result?

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

Also, could you please specify the assembly progress and update the step-by-step instructions?

As the [STLs](https://github.com/kg398/100_fingers/tree/main/STLs) includes multiple folder and files, could you specify the corresponding version between several folders?

kg398, 2025-05-23:
Hello,

The warning shouldn't be an issue for 3d printing. Though you should inspect the sliced stl particularly around the joints and tendon paths to make sure there are nice continuous lines everywhere.

For assembly, the main job is tendon routing especially in the actuation system. This is something we are currently working to improve and provide more detailed assembly instructions for, but you can use the existing actuation system as an example method of holding all tendons in tension and actuating a subset of them.

I can give some general tips for assembly and try to answer any specific questions you have. The recommended process is to first prepare the hand with all tendons, there will be six per finger (with one pair on the extensor side terminating into a single tendon). Make sure these are secured to the four anchor points on each finger (if the knots unravel a very small amount of superglue can help). I find it easiest to assemble the passive tendons into the actuation box next, which you can leave partially disassembled for easier access. The provided spring clips to connect tendons to springs are easier to work with if once you pull the tendon to the desired length you clamp it in place or wrap it around a spare bolt on the assembly box so you can use two hands to fasten the clip. To attach the springs I make a 55mm detaining pin out of 1.5mm rod but you can use m2 threaded rod, long screws, or even wire/filament. The active tendons are in much need of improvement for ease of assembly, especially into the 5-to-1 pulley. I find it helpful to lock the pulley into place using some of the extra holes in the actuation box and once threading tendons over their respective pulleys and to the anchor bolts, just wrapping around twice and tightening down is usually enough to hold them in place.

Good luck with the hand and if you want I can keep you updated when we release the easier to assemble version and build instructions.

Thanks,
Kieran
________________________________
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

minnyqiu, 2025-06-06:
Hi, Kieran.

Thanks so much for the specific instruction. I tried to use the PA12 to print the human hand part, and the junction from palm to fingers is easy to break, so I am still trying to adjust the thickness to make sure the printed hand is complete. Anyway, thanks so much to your team for bringing this fantastic work and for your kind help.

kg398, 2025-07-15:
Hello Minny,

The initial step-by-step instructions are now complete and uploaded. Also the new release contains some features to make the assembly process easier.

For printing with PA12, I was successful printing before once with ligament thickness 0.8mm. Thicker and the joints get too stressed with repeated bending. If the issue is the high bending to go from extended ligaments after printing to flexed in the joint socket, then you could try setting the joints while the ligaments are above the glass transition temperature. Easy way is pour some boiled water over the ligaments, bend them, and let them cool one at a time.

Hopefully this is helpful.

Thanks,
Kieran

minnyqiu, 2025-07-17:
Hi Kieran,

Thanks so much for your detailed instrucitons.

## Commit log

2023-02-21 improved pulleys
    [digits.scad, finger_50-40-35-25_12-10-8_45_5-1.5-1.stl, hand.scad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]
2023-02-22 fixed includes
    [digits.scad, hand.scad]
2023-03-07 fixed files, minor hand updates
    [hand.scad, hand_test3.stl, parameters.scad]
2024-01-16 generating_v3
    small restructuring, changed flex pulleys for adaptive joint stability, qol tendon anchors, no lig version for renders, human_hand_v3 params
    [digits.scad, finger_test.stl, hand.scad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]
2024-07-05 Actuation CAD and media examples
    Starting to organise and update files for first release version
    [hand_couple.stl, handle.stl, handle_double.stl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]
2024-07-05 organising for release
    [daubentonia_v3.stl, digits.scad, double_thumb_v3.stl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]
2024-08-22 Update with designs inspired by OPH design space
    [parameters.scad, random_examples.scad]
2025-01-08 generating from local version 4.1
    Improved MCP design
    Combined finger/thumb modules
    New parametric pulley file
    [digits.scad, hand.scad, parameters.scad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]
2025-01-10 Overtaken release 1.1
    Updated joints and parameterisation for greater customisability in abduction and better behaviours.
    New hand module for printing individual fingers/palm.
    [hand.scad, human_hand_v4.stl, parameters.scad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]
2025-01-10 minor remodeling
    Increased rack thickness. Cleaned pulley_base. Option for angled back wrist.
    [bearing_block.stl, lightweight_pulley v4.stl, panel_left.stl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]
2025-07-01 OPH improved joints, fixes, 1DoF
    Bug fixes in ligament length, extensor routing fillets, and thumb opposition pulley.
    New pulley design with fast tendon tuning.
    Updated 1DoF actuation box and handle for easier assembly
    [bearing_block.stl, digits.scad, hand_couple.stl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]
2025-07-14 missing updated files
    [pulley_base.stl, sea.stl]
2025-09-26 qol update for 2dof box
    now matching 1dof version
    [bambu_plate.3mf, hand_couple.stl, pulley.stl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]
2025-12-10 Overhaul of parameter definitions and how bones are generated
    Redefined parameter structure into lists of finger and thumb params. Included 2 new high level params (no. fingers and no. thumbs) for more flexibility with number of digits. Overhauled bone generati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
    [digits.scad, hand.scad, parameters.scad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]
2025-12-10 default hand
    [parameters.scad]
2025-12-17 Initial skin update
    One abd pulley location bug fixed
    Added assembly jig holes and corresponding config options (assembly jig to follow)
    Aligned prototype multimaterial skin with new plugin (currently only works with default finger/hand configs)
    [digits.scad, parameters.scad, primitives.scad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]
